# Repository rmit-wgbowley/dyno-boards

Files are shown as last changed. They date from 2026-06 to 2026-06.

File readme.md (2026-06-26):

<p align="center">
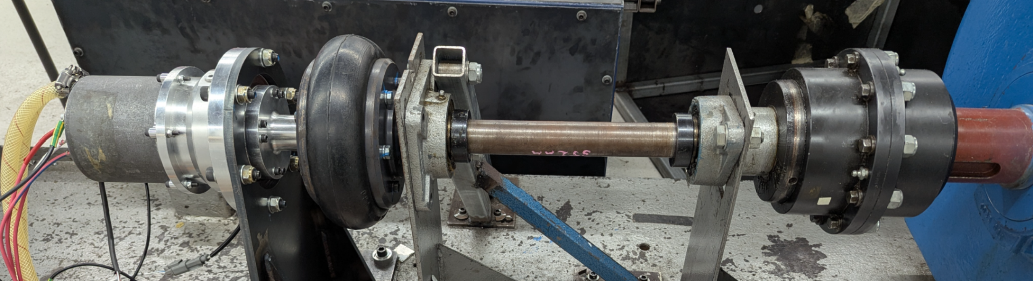
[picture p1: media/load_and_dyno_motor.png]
load_and_dyno_motors
  
</p>

## Overview




The RMIT dyno setup consists of two systems, the dyno controller panel (DCS800) and r19e/r26 ECU. This allows for the car's powertrain system to be validated before implementation into the car. The ECU controls the load motor and HV system. However, for this test setup it is also meant to transmit a `0-3.3 V @ 10 kHz` PWM signal to control the dyno motor RPM. This allows for a lookup table to be used to ramp up the dyno motor (former elevator motor) RPM in an arbitrary function.

> [!NOTE]
> ECU-side board can be found [here](ecu-side) & dyno-side board can be found [here](dyno-side).

## Why communicate? 

The 2026 dyno setup uses speed control on the dyno-side and torque control on the load motor. This allows for a lookup table to be used to ramp up the dyno RPM to model RPM vs torque. For example, the dyno-side RPM over time could be modelled as this arbitrary function:

$$ RPM(t) = \frac{A}{2B}(1-\cos(\frac{\pi t}{t_{total}})), \quad RPM(t) \in [0, dyno_{max}] $$

Where `A` is the target RPM at the load side, `B` is the gearing ratio between the dyno motor and load motor, and `t_total` is the total time to reach that requested RPM. The requested RPM then needs to be converted to duty cycle:

$$ DC(t) = (\frac{C \times RPM(t)}{2})(\frac{3.3}{5})(\frac{100}{3.3})$$
$$ DC(t) = 10C \times RPM(t), \quad DC(t) \in [0, 100]$$

And then it would simply be transformed into a simple lookup table, assuming `C` is the dyno controller input scaling factor `(V/RPM)` after the 2× amplification stage.

> [!important]
> The dyno has a `200 kΩ` input impedance (AI1), an analog range of `0–10 V` with a linear factor of `5 mV/RPM`, and a maximum safe RPM of `1800` at the dyno-side motor. The r26 powertrain has a gearing of `1:12.81`. Driving frequency table (ARR), output ripple at the dyno, and duty-cycle resolution trade-offs can be found [here](domain-side/readme.md).

| Step | Time (s) | ECU Duty Cycle (%) | Dyno Controller Input (V) | Target Dyno (RPM) | Target Load (RPM) |
| :--- | :---: | :---: | :---: | :---: | :---: |
| 0 | 0.00 | 0.00 | 0.0  | 0  | 0 |
| 1 | 0.25 | 0.26 | 0.03 | 5  | 64 |
| 2 | 0.50 | 0.98 | 0.10 | 20 | 256 | 
| 3 | 0.75 | 1.95 | 0.20 | 39 | 500 |
| 4 | 1.00 | 2.93 | 0.29 | 59 | 755 |
| 5 | 1.25 | 3.64 | 0.36 | 73 | 935 |
| 6 | 1.50 | 3.90 | 0.39 | 78 | 999 |

*Figure 1: Example profile parameters configured for a real-time `1.5-second` window with time steps of `250 ms` using `A = 1000`, `B = 12.81`, and `c = 0.005`.*

> [!note]
> The program used to generate that table can be found [here](domain-side/example_profiles.py)

However, for the real system, race day data is used to model the dynamic torque loading on the load motor. 

## High-level Topology

The dyno controller and r19e ECU are approximately `2-4 meters` apart and operate at different voltage levels (`0-3.3V` vs `0-10V`). So an ECU conditioning/isolation board is used, and a dyno receiver/amplification board is used.

```
Interface (2.54mm Pitch Male Header)
ECU PWM Source (Digital 3.3 V - PB13, tim1_CHN1, STM32F405RGT6)
                    ↓

Interface (JST XH 4-pin 2.5mm)
ECU Side (3.3 V logic / 5 V domain) (conditioning / isolation)
--------------------------------------------
Schmitt trigger (Cleans up the signal edge)
    ↓
Digital Isolator (Isolates the PWM signal) ← (Isolated 5 V domain)
    ↓
RS-422 Driver (A/B differential pair)
-------------------------------------------- 
Interface Socket (RJ45)
                    ↓

CAT 5/6 Cable
--------------------------------------------
twisted pairs: (+signal, -signal)
--------------------------------------------
                    ↓

Interface Socket (RJ45)
DYNO Side (5 / 10 V domain) (receiver / amplification) 
--------------------------------------------
RS-422 receiver (Differential input, rejects noise) ← (5 V LDO)
    ↓
RC low-pass filter (50 Hz) (PWM to DC voltage conversion)
NOTE:
Ripple magnitude depends on PWM frequency,
filter capacitance, and filter resistance.
    ↓
Op-amp 2× Gain (non-inverting) (Scales to 0–10V ADC input range) ← 10 V Line
--------------------------------------------- 
Interface (JST XH 4-pin 2.5mm)
                    ↓
Interface (4-pin barrel jack) (Unknown Specifics)
DYNO Controller (Analog 10V Input)
```

## Hardware Photo

<p align="center">
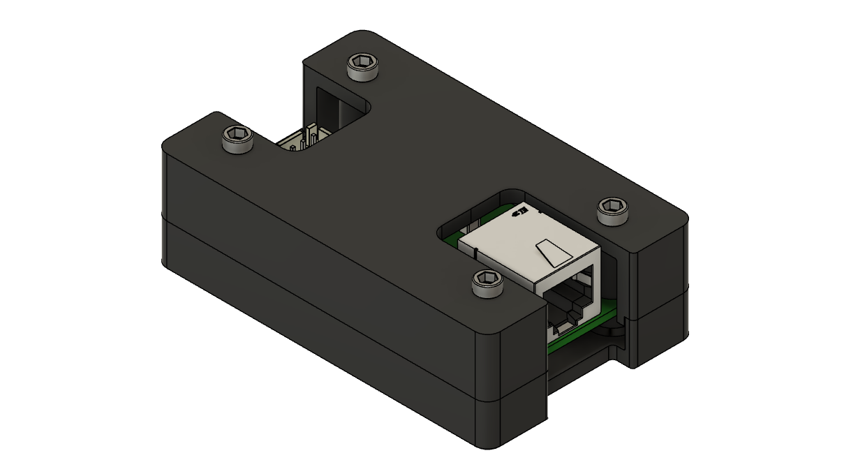
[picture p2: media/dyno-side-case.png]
Dyno-side case render
  
</p>
<p align="center">
  <em>Housing design (identical for both ECU-side and Dyno-side boards)</em>
</p>

> [!NOTE]
> Case design files: [Available here (Fusion source files)](domain-side/pcb_case/)
> - Same case size and external design for both boards — only internal PCBs differ
> - IGES format included for users without Fusion
> - 4× M3 inserts for mounting PCB and top housing
> - Velcro recommended to secure the housing to the test bench

## Documentation

All internal documentation can be found within this repo's [issues](https://github.com/rmit-wgbowley/dyno-boards/issues?q=state%3Aclosed).

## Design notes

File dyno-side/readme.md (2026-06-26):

### Dyno Side Topology & Components

```
Interface (RJ45) 
ECU Side (5V PMW twisted pairs: +signal, -signal)
                    ↓
Interface (RJ45) 
DYNO Side (5/10 V domain) (receiver / amplification) 
--------------------------------------------
5V Line ← (TPS7A4901, 14 ms start-up, 0.1–0.5 W | R1 = 10 kΩ & R2 = 33 kΩ)
    ↓
RS-422 receiver (Differential input, rejects noise) (AM26LS32AIN)
    ↓
RC low-pass filter (50 Hz) (PWM to DC voltage conversion)
    ↓
Op-amp 2× Gain (Scales to 0–10 V) (TLV272) ← 10 V Line
---------------------------------------------
Interface (JST XH 4-pin 2.5 mm)
                    ↓
Interface (4-pin barrel jack) (Unknown Specifics)
DYNO Controller (Analog 10V Input)
```

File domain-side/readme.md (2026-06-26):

# Output Dynamics Based on Frequency Changes (FOR STM32F405RGT6)

> [!important]
> Assumed Configuration:
> - PSC = 0
> - RC Characteristics: 2 kΩ, 1.6 µF
> - Clock Speed: 160 MHz on TIM1_CH1N (APB2)
> - APB2 (Scale of 2x) → PCLK2 (80 MHz) → 160 MHz
> - These values will be different if R7 and C9 are populated with (47 Ω | 100 nf, etc.)

## Initial Calibration Row (10 kHz)

| RPM Step (at Dyno) | ARR | Frequency | Output Ripple (After 2x @ DYNO) |
|---|-----|---|---|
| 0.625 rpm | 15999 | 10.000 kHz | 156.080 mV |

## Main Table (0.2 rpm Resolution)

| RPM Step (at Dyno) | ARR | Frequency | Output Ripple (After 2x @ DYNO) |
|---|-----|---|---|
| 0.200 rpm | 9999 | 16.000 kHz | 97.656 mV |
| 0.400 rpm | 4999 | 32.000 kHz | 48.828 mV |
| 0.600 rpm | 3332 | 48.005 kHz | 32.549 mV |
| 0.800 rpm | 2499 | 64.000 kHz | 24.414 mV |
| 1.000 rpm | 1999 | 80.000 kHz | 19.531 mV |
| 1.200 rpm | 1666 | 95.981 kHz | 16.279 mV |
| 1.400 rpm | 1428 | 111.966 kHz | 13.955 mV |
| 1.600 rpm | 1249 | 128.000 kHz | 12.207 mV |
| 1.800 rpm | 1110 | 144.014 kHz | 10.850 mV |
| 2.000 rpm | 999 | 160.000 kHz | 9.766 mV |
| 2.200 rpm | 908 | 176.018 kHz | 8.877 mV |
| 2.400 rpm | 832 | 192.077 kHz | 8.135 mV |
| 2.600 rpm | 768 | 208.062 kHz | 7.510 mV |
| 2.800 rpm | 713 | 224.090 kHz | 6.973 mV |
| 3.000 rpm | 666 | 239.880 kHz | 6.514 mV |
| 3.200 rpm | 624 | 256.000 kHz | 6.104 mV |
| 3.400 rpm | 587 | 272.109 kHz | 5.742 mV |
| 3.600 rpm | 555 | 287.770 kHz | 5.430 mV |
| 3.800 rpm | 525 | 304.183 kHz | 5.137 mV |
| 4.000 rpm | 499 | 320.000 kHz | 4.883 mV |
| 4.200 rpm | 475 | 336.134 kHz | 4.648 mV |
| 4.400 rpm | 454 | 351.648 kHz | 4.443 mV |
| 4.600 rpm | 434 | 367.816 kHz | 4.248 mV |
| 4.800 rpm | 416 | 383.693 kHz | 4.072 mV |
| 5.000 rpm | 399 | 400.000 kHz | 3.906 mV |
| 5.200 rpm | 384 | 415.584 kHz | 3.760 mV |
| 5.400 rpm | 369 | 432.432 kHz | 3.613 mV |
| 5.600 rpm | 356 | 448.179 kHz | 3.486 mV |
| 5.800 rpm | 344 | 463.768 kHz | 3.369 mV |
| 6.000 rpm | 332 | 480.480 kHz | 3.252 mV |
| 6.200 rpm | 322 | 495.356 kHz | 3.154 mV |
| 6.400 rpm | 311 | 512.821 kHz | 3.047 mV |
| 6.600 rpm | 302 | 528.053 kHz | 2.959 mV |
| 6.800 rpm | 293 | 544.218 kHz | 2.871 mV |
| 7.000 rpm | 285 | 559.441 kHz | 2.793 mV |
| 7.200 rpm | 277 | 575.540 kHz | 2.715 mV |
| 7.400 rpm | 269 | 592.593 kHz | 2.637 mV |
| 7.600 rpm | 262 | 608.365 kHz | 2.568 mV |
| 7.800 rpm | 255 | 625.000 kHz | 2.500 mV |
| 8.000 rpm | 249 | 640.000 kHz | 2.441 mV |
| 8.200 rpm | 243 | 655.738 kHz | 2.383 mV |
| 8.400 rpm | 237 | 672.269 kHz | 2.324 mV |
| 8.600 rpm | 232 | 686.695 kHz | 2.275 mV |
| 8.800 rpm | 226 | 704.846 kHz | 2.217 mV |
| 9.000 rpm | 221 | 720.721 kHz | 2.168 mV |
| 9.200 rpm | 216 | 737.327 kHz | 2.119 mV |
| 9.400 rpm | 212 | 751.174 kHz | 2.080 mV |
| 9.600 rpm | 207 | 769.231 kHz | 2.031 mV |
| 9.800 rpm | 203 | 784.314 kHz | 1.992 mV |
| 10.000 rpm | 199 | 800.000 kHz | 1.953 mV |

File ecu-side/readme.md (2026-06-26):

### ECU-side Topology & Components

```
Interface (2.54mm Pitch Male Header)
ECU PWM Source (Digital 3.3 V @ 10 kHz - PB13, tim1_CHN1, STM32F405RGT6)
                    ↓
Interface (JST XH 4-pin 2.5mm)
ECU Side (3.3 V logic / 5 V domain) (conditioning / isolation)
--------------------------------------------
Schmitt trigger (Cleans up the signal edge) (SN74LVC1G17)
    ↓
Digital Isolator (Isolates the PWM signal) (ISO7720) <- RFM-0505S (isolated 5 V)
    ↓
RS-422 Driver (A/B differential pair) (AM26LS31)
--------------------------------------------
Interface Socket (RJ45) (twisted pairs: +signal, -signal)
                    ↓
Interface (RJ45) 
DYNO Side (5/10 V domain) (receiver / amplification) 
```

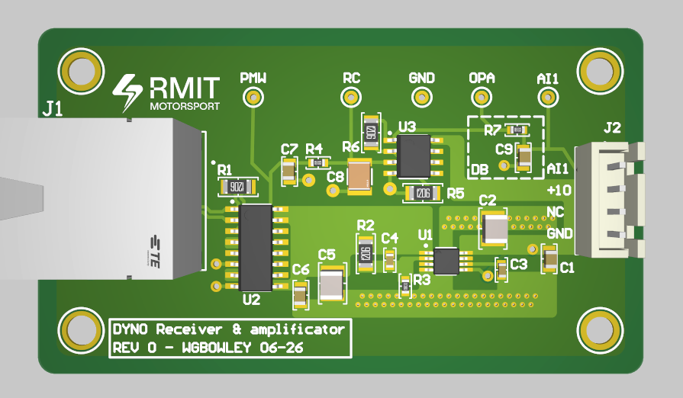
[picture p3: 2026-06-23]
dyno-side/pcb_design_rev_0.png

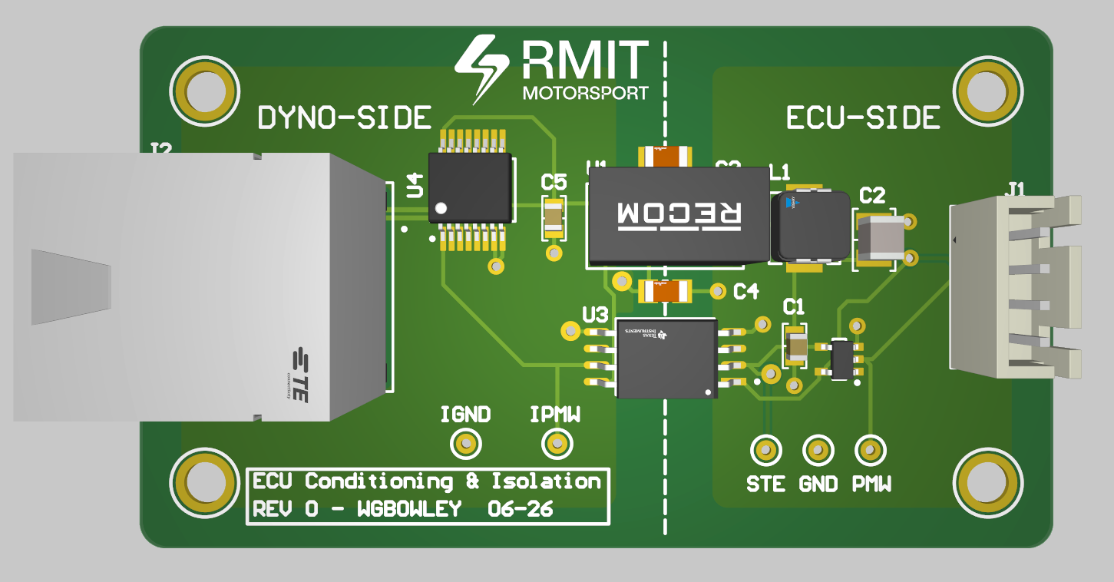
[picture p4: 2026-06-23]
ecu-side/pcb_design_rev_0.png

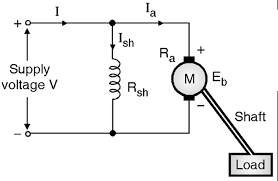
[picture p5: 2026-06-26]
media/dyno-motor-topology.png

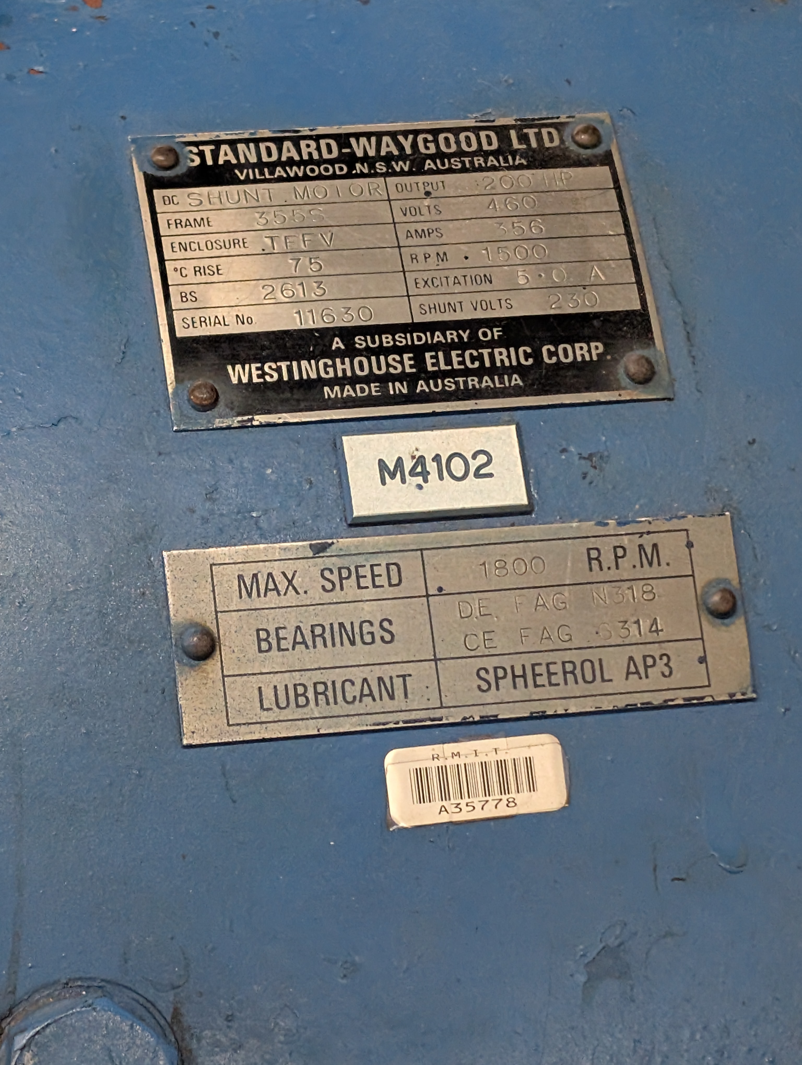
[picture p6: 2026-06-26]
media/dyno-motor.jpg

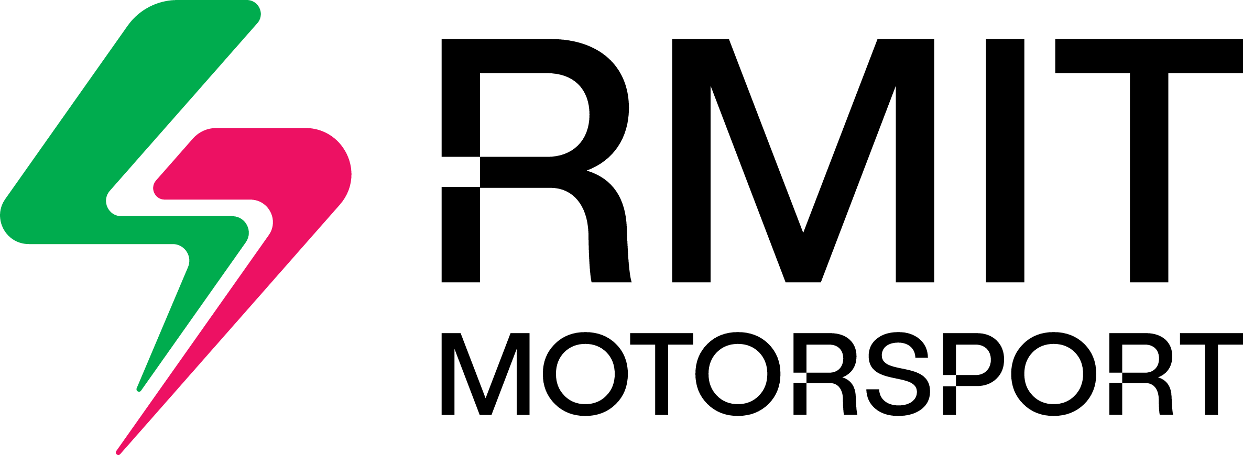
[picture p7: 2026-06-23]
media/RMIT Motorsport Black.png

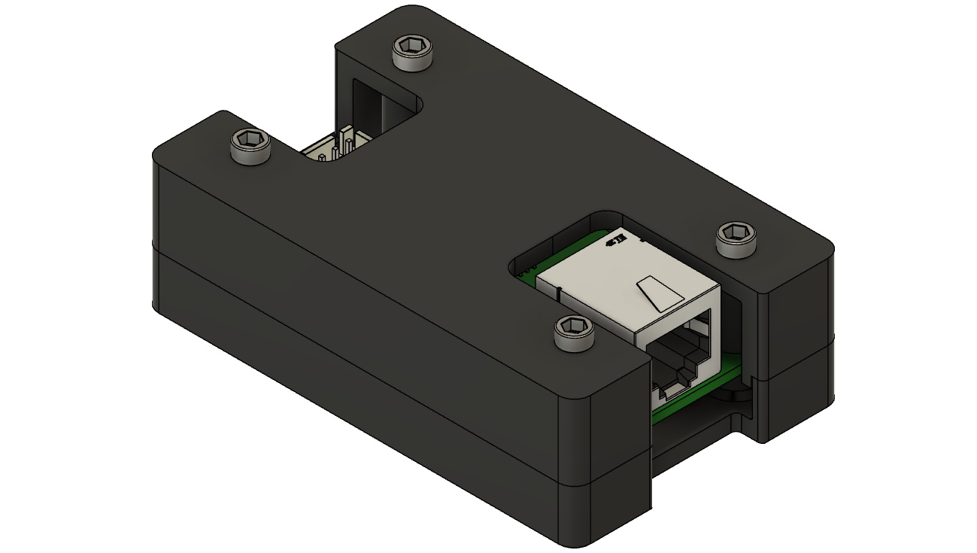
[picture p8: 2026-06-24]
media/ecu-side-case.png

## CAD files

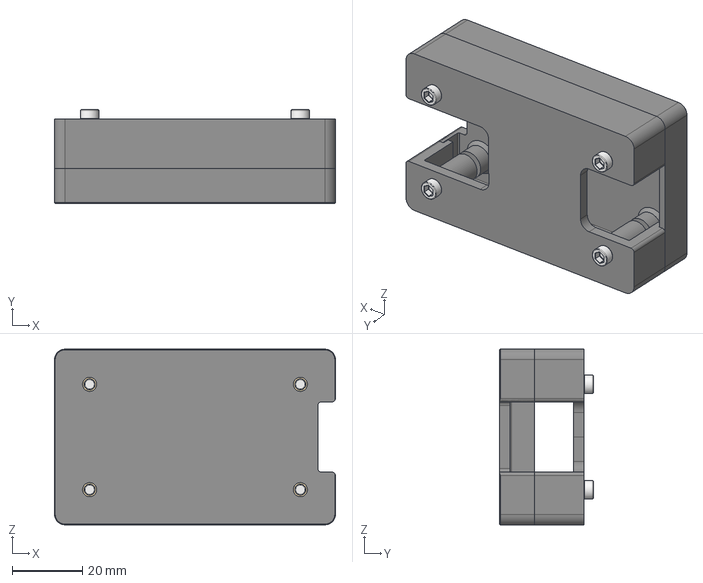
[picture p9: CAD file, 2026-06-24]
domain-side/pcb_case/pcb_case.iges
80.0 x 26.7 x 50.0 mm

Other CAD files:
domain-side/pcb_case/pcb_case.f3z

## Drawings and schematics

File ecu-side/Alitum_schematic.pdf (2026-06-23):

REVISION | DESCRIPTION | DATE | APPROVED | REV. SHT. DWG. NO. 1

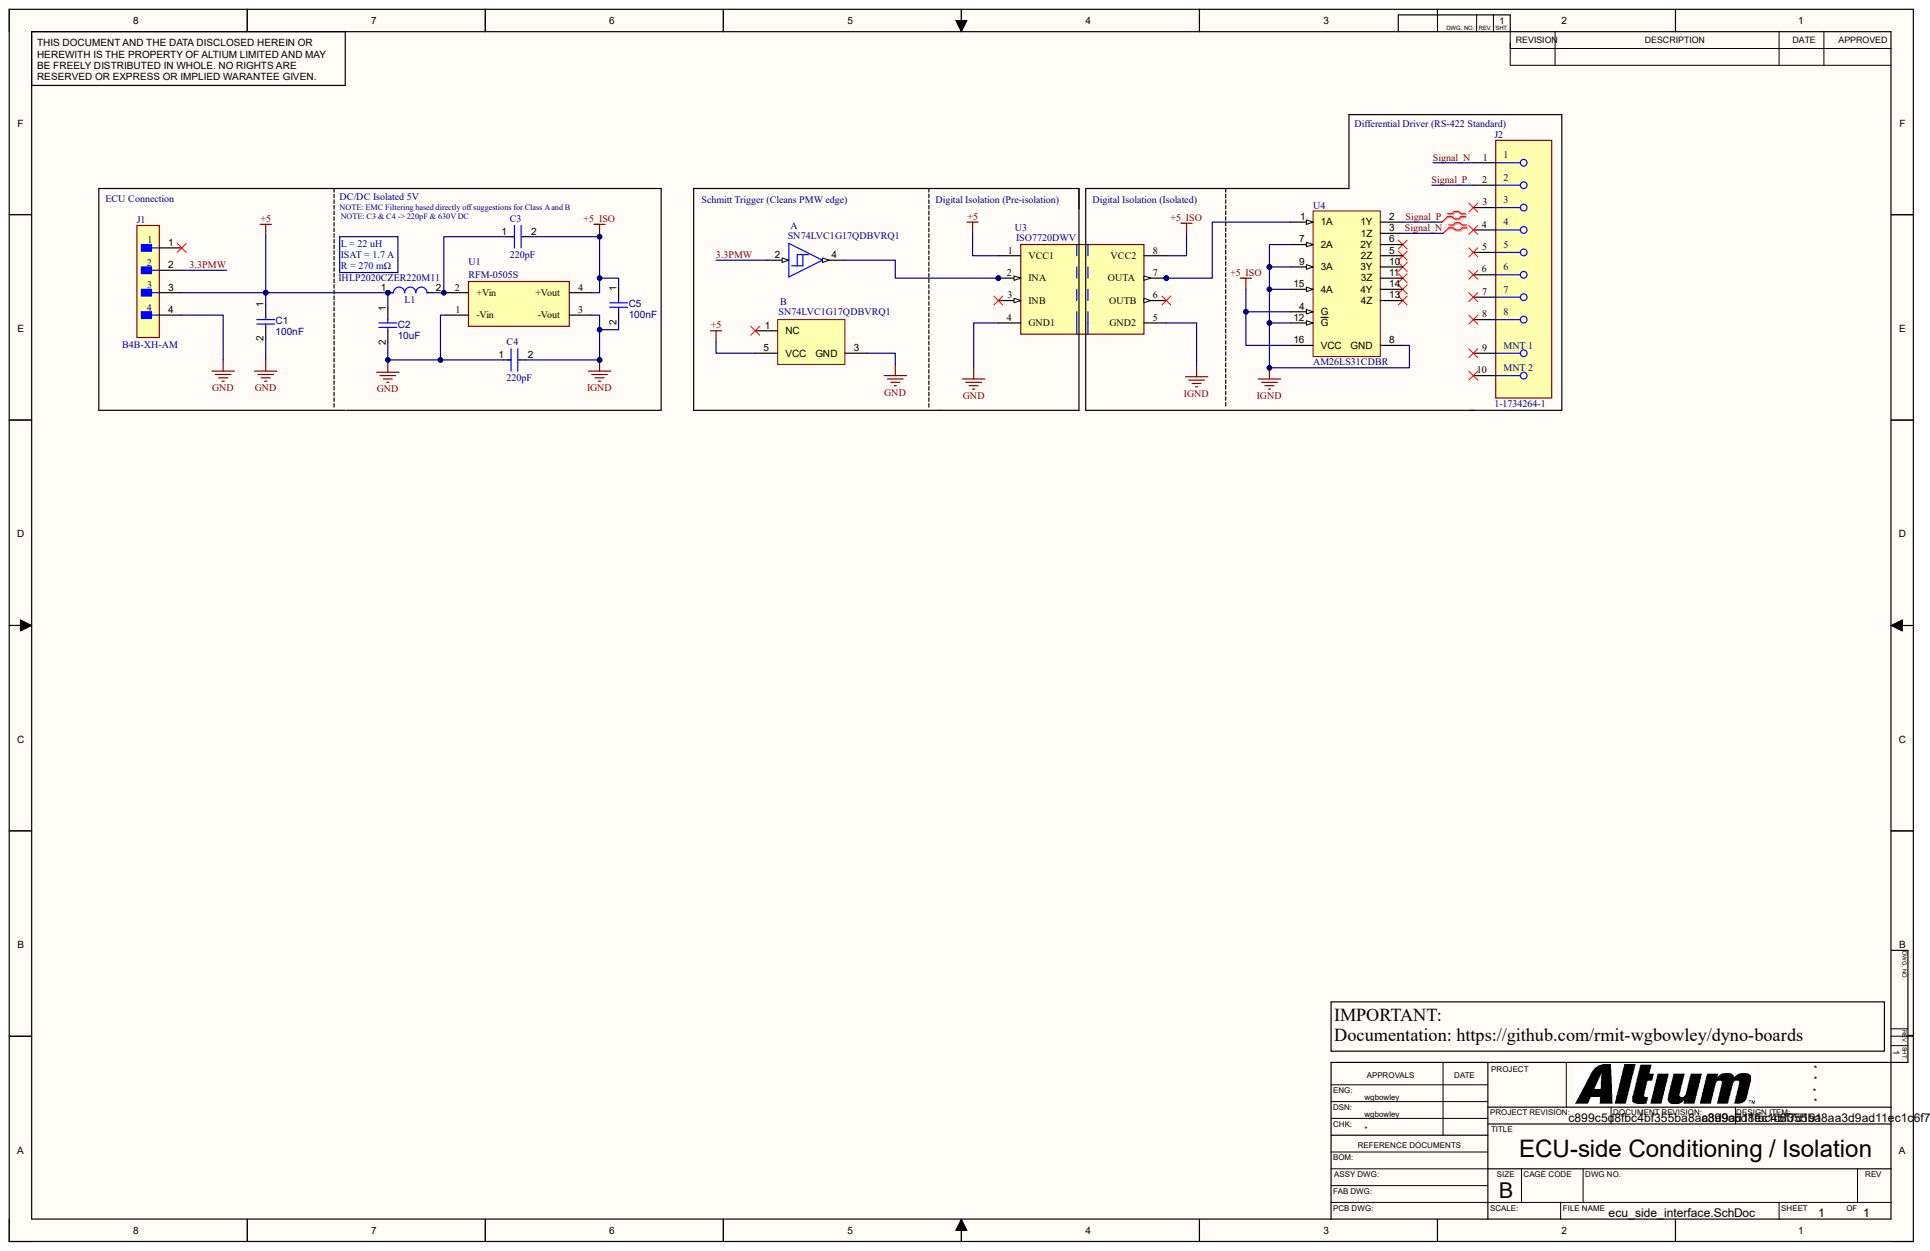
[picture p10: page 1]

THIS DOCUMENT AND THE DATA DISCLOSED HEREIN OR
HEREWITH IS THE PROPERTY OF ALTIUM LIMITED AND MAY
BE FREELY DISTRIBUTED IN WHOLE. NO RIGHTS ARE
RESERVED OR EXPRESS OR IMPLIED WARANTEE GIVEN.

Differential Driver (RS-422 Standard)

Schmitt Trigger (Cleans PMW edge)

Digital Isolation (Pre-isolation)

NOTE: EMC Filtering based directly off suggestions for Class A and B 1 2

IMPORTANT:
Documentation: https://github.com/rmit-wgbowley/dyno-boards

APPROVALS | DATE | PROJECT | * *

ENG: wgbowley
CHK: * | | TITLE ECU-side Conditioning / Isolation

DSN: wgbowley

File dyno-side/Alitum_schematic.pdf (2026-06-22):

REVISION | DESCRIPTION | DATE | APPROVED | REV. SHT. DWG. NO. 1
IN 8 | 9

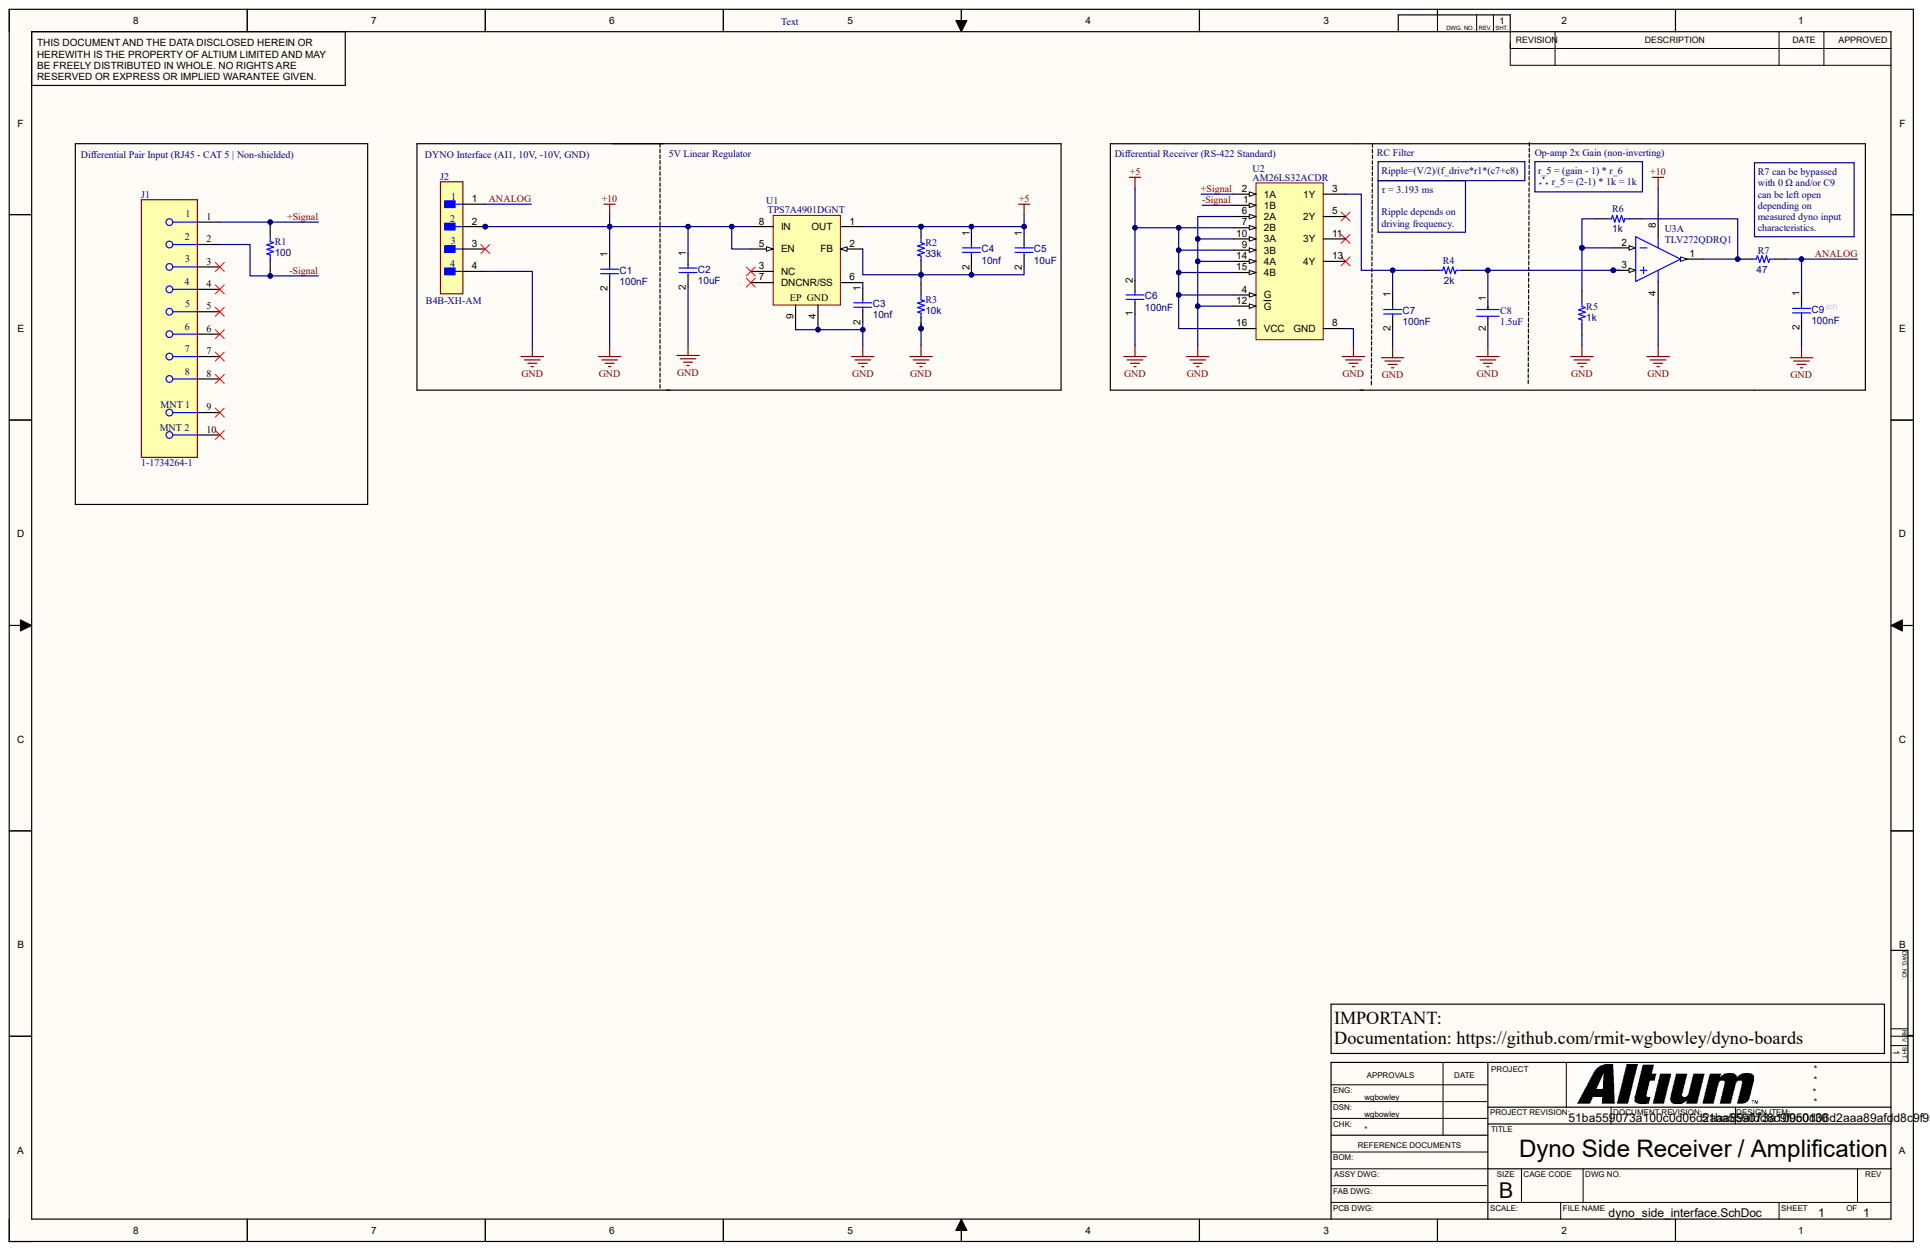
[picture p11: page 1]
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

Differential Pair Input (RJ45 - CAT 5 | Non-shielded)

R7 can be bypassed
with 0 Ω and/or C9
can be left open
depending on
measured dyno input
characteristics.

IMPORTANT:
Documentation: https://github.com/rmit-wgbowley/dyno-boards

APPROVALS | DATE | PROJECT | * *

ENG: wgbowley
CHK: * | | TITLE Dyno Side Receiver / Amplification

DSN: wgbowley

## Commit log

2026-05-30 Comment out ECU conditioning board explanation
    Commented out a section explaining the ECU conditioning board and signal processing.
2026-06-04 dyno side schematic + simulation
    [AM26LS32ACN.step, dyno-side.kicad_pcb, dyno-side.kicad_sch]
2026-06-05 schematics finished -> Waiting for Altium membership to be progressed.
    [AM26LS31CN.step, RFM-0505S.step, SN74LVC1G17.step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]
2026-06-05 Adding component readmes for each board. Also placeholder for alitum.
2026-06-05 corrections tlv9002 replaced with lm458 & ecu 5v domain not 3.3v domain.
    [dyno-side.kicad_sch, ecu-side.kicad_sch]
2026-06-07 Fixed op-amp mistake (wrong source) & deceased op-amp output impedance.
    [dyno-side.kicad_sch]
2026-06-15 Beginning design of schematics in Altium desginer
    [dyno-side-schematic.SchDoc, ecu-side-schematic.SchDoc]
2026-06-16 dyno-side board schematic edits
    [dyno-side-schematic.SchDoc]
2026-06-18 Continuing work on dyno schematic in Altium
    [dyno-side-schematic.SchDoc]
2026-06-19 domain modelling and dyno controller checks
    [AM26LS31CN.step, AM26LS32ACN.step, RFM-0505S.step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]
2026-06-21 Updates to readme & removing .schDoc temporarily
    [dyno-side-schematic.SchDoc, ecu-side-schematic.SchDoc]
2026-06-21 Dyno-side Schematic & Validation Finished
2026-06-22 Different ARR values & final schematic for dyno-side
2026-06-23 ecu and dyno pcbs done -> case design and finished for review :)
2026-06-24 universal PCB case design and PCB .step files
    [pcb_case.f3z, pcb_case.iges]

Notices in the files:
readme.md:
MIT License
